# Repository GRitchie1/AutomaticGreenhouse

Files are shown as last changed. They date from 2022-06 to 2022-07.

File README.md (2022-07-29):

# AutomaticGreenhouse

## Introduction
This project is to design and build a solar powered outdoor greenhouse that can monitor and control the temperature & humidity of the air as well as automatically water the plants using collected rainwater.

The design of this project is intended to be highly modular, with the ability to chain multiple target nodes (units) together to allow for data to be combined and analysed by a single controller node.  The power supply from the solar power system will also be chained to allow for a more simple power distribution setup.

## Contents
| Topic | Description |
|---|---|
| [Design](#design) | An overview of the design of the project |
| [Monitoring](#monitoring) | An overview of the design of the project |
| [Parts Lists](#parts-lists) | Up to date parts lists for the project |
| [PCBs](#pcbs) | Information regarding the design and manufacture of the custom printed circuit boards |
| [Networking](#networking) | Information regarding the communication between the target nodes and the controller node. |

## Design
Each target node in the system will be based upon a Raspberry Pi Pico and all hardware interfacing will be done using a custom PCB.  The controller node will be a Raspberry Pi 4 managed using [Balena](https://www.balena.io/).  Communication between the target nodes and the controller node is documented in [networking](#networking).

Each node will feature space for 6 planters, and will have a modular irrigation system to allow for planters to be easily added and removed.

Each node will feature the following sensors:
- Temperature
- Air Humidity
- Soil moisture sensors (1 per planter)
- Light Level (front and back of unit)
- Water level to monitor irrigation system
- Camera (optional: adds ability to implement timelapses and machine learning)

Each node will feature the following control systems:
- Light (LED strips)
- Temperature/Humidity (DC Fan)
- Soil moisture (Water Solenoid/Pump)

An overview of the system layout can be seen below.
System Overview

## Monitoring 

Currently monitoring is done using InfluxDB and Grafana running on a Raspberry Pi 4B.  This is also running an MQTT broker and is using Node-Red to recieve and sanitize the telemetry before inserting it into InfluxDB.

The current Grafana dashboard can be seen below.



## Parts Lists

**Note the following parts lists are not complete and may change.**

The following parts are required to build one node PCB.

| Part | Qty | Description |
|---|-----|---|
| [Pi Pico](https://thepihut.com/products/raspberry-pi-pico) | 1  |The microcontroller used to control the node. |
| [TCA9548A I2C Multiplexer](https://thepihut.com/products/adafruit-tca9548a-i2c-multiplexer)  | 1  | I2C multiplexer to allow connection of up to 8 soil humidity sensors with the same I2C address  |
| N-Channel Mosfet | 5 | Control outputs |

The following sensors are required to build one node.

| Sensor | Qty | Description |
|---|-----|---|
| [Temperature/Humidity](https://thepihut.com/products/adafruit-sensiron-sht31-d-temperature-humidity-sensor-breakout) | 1 | Monitor air temperature and humidity in the greenhouse. |
| [Soil Humidity](https://thepihut.com/products/adafruit-stemma-soil-sensor-i2c-capacitive-moisture-sensor-ada4026) | 6 | Monitor soil humidity of each planter. |
| Light Sensor | 2 | Monitor wavelengths of light to optimise growth. |
| Water Level Switch | 1 | Monitor the stored water level to trigger an alert if it gets too low. |

## PCBs
The PCBs are designed in [EASYEDA](https://easyeda.com/) and can be ordered from [JLC PCB](https://jlcpcb.com/).

The parts for the PCBs can be found in the [Parts Lists](#parts-lists).

## Networking
The communication between the target nodes and the controller node will be handled using MQTT over Ethernet.

The controller node will act as an MQTT broker and also as a client.  Each of the target nodes will be provisioned with unique ID's by the controller node using the following procedure:
1. Target node generates random ID, uses this as Client ID
2. Target node sends "Connection Request" mqtt message to the controller node on topic greenhouse/{Client ID/connection.
3. Target node begins listening on topic greenhouse/{Client ID}/response
4. The Controller node verifies the target node can connect, and returns a new production ID on the topic greenhouse/{Client ID}/response
5. The Target node stores this production ID in the EEPROM and uses this as it's client ID

This procedure ensures that the Controller node can always identify the Target node even after restarts.  It also means that if a Target node PCB is replaced, the new Target node PCB can be programmed with the correct client ID so that the data remains consistent for that unit.

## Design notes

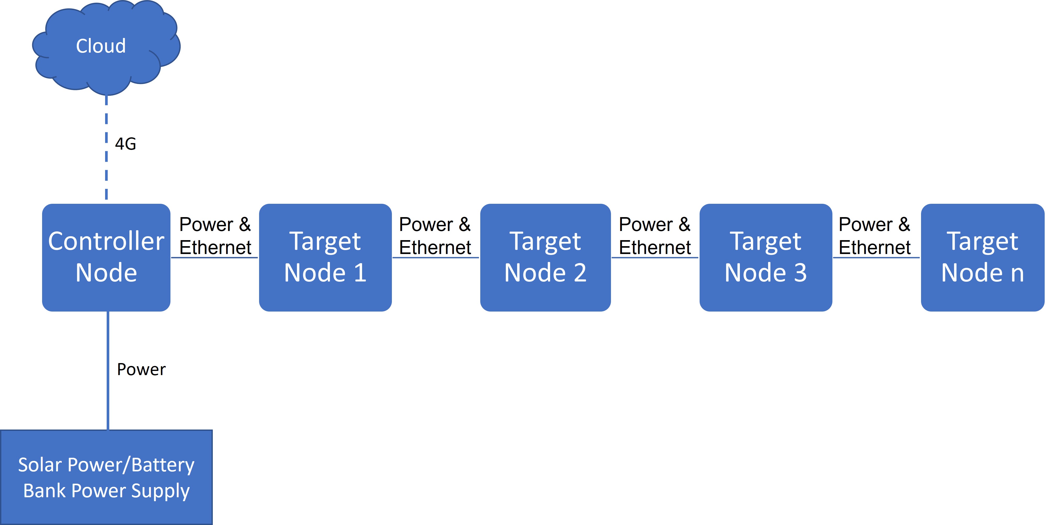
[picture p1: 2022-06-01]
Images/System Overview.jpg

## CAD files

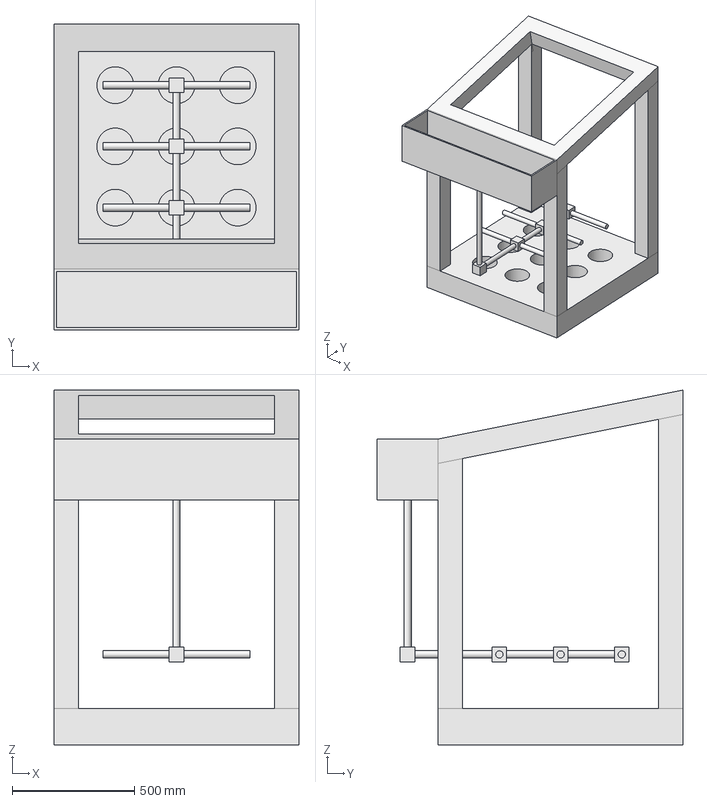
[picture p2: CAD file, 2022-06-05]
3D Model/Frame.FCStd
1000.0 x 1250.0 x 1450.0 mm

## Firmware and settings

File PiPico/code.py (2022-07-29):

import time
import board
import adafruit_sht31d
import busio
import digitalio
import json
import adafruit_veml7700
import adafruit_tca9548a
from adafruit_seesaw.seesaw import Seesaw

#Setup
deviceID = "AutoGH_1"
control = {
            'minSoilHumid':500,
            'maxAirHumid':70
            }


### MQTT ###
from adafruit_wiznet5k.adafruit_wiznet5k import *
import adafruit_wiznet5k.adafruit_wiznet5k_socket as socket
import adafruit_minimqtt.adafruit_minimqtt as MQTT

#Ethernet
##SPI0
SPI0_SCK = board.GP18
SPI0_TX = board.GP19
SPI0_RX = board.GP16
SPI0_CSn = board.GP17


##reset
W5x00_RSTn = board.GP20

pubTopic = 'AutoGH/data'
subTopic = 'AutoGH/control'
mqtt_client = MQTT.MQTT(
    broker="192.168.1.109",  #setup your PC IP address.
    username="iotdash",
    password="iotdash",
    is_ssl=False,
    socket_pool=None,
    ssl_context=None,
    keep_alive=60,
)

def recieveMessage(client, topic, newControl):
    global control
    newControl = json.loads(newControl)
    if newControl != control:
        control = newControl

MY_MAC = (0x00, 0x01, 0x02, 0x03, 0x04, 0x05)
IP_ADDRESS = (192, 168, 1, 100)
SUBNET_MASK = (255, 255, 255, 0)
GATEWAY_ADDRESS = (192, 168, 1, 1)
DNS_SERVER = (8, 8, 8, 8)

ethernetRst = digitalio.DigitalInOut(W5x00_RSTn)
ethernetRst.direction = digitalio.Direction.OUTPUT

cs = digitalio.DigitalInOut(SPI0_CSn)

spi_bus = busio.SPI(SPI0_SCK, MOSI=SPI0_TX, MISO=SPI0_RX)

ethernetRst.value = False
time.sleep(1)
ethernetRst.value = True

eth = WIZNET5K(spi_bus, cs, is_dhcp=True, mac=MY_MAC, debug=False)

print("Chip Version:", eth.chip)
print("MAC Address:", [hex(i) for i in eth.mac_address])
print("My IP address is:", eth.pretty_ip(eth.ip_address))

MQTT.set_socket(socket, eth)

mqtt_client.on_message = recieveMessage

print("Connecting to Broker...")
mqtt_client.connect()

### Sensors ###
i2c = busio.I2C(board.GP5, board.GP4)    #Init I2C

tempHumid = adafruit_sht31d.SHT31D(i2c)
veml7700 = adafruit_veml7700.VEML7700(i2c)

#Soil Sensors
tca = adafruit_tca9548a.TCA9548A(i2c)
numSoilSensors = 3
soilSensors=[Seesaw(tca[i], addr=0x36) for i in range(numSoilSensors)]

### Outputs ###
#Water Pump
pump = digitalio.DigitalInOut(board.GP2)
pump.direction = digitalio.Direction.OUTPUT

#Water Pump
fan = digitalio.DigitalInOut(board.GP3)
fan.direction = digitalio.Direction.OUTPUT

#Vars
loopcount = 0

while True:
    mqtt_client.loop()
    mqtt_client.subscribe(subTopic)
    loopcount += 1

    obj={}
    obj['ID'] = deviceID
    obj['control']=control

    #Env Sensors
    obj['temp'] = tempHumid.temperature
    obj['humid'] = tempHumid.relative_humidity
    obj['light'] = veml7700.light

    #Read Soil Sensors
    soilData = []
    totalSoilHumid = 0
    for sensor in soilSensors:
        soilObj = {}
        soilObj['soilMoisture'] = sensor.moisture_read()
        soilObj['soilTemp'] = sensor.get_temp()
        soilData.append(soilObj)
        totalSoilHumid += soilObj['soilMoisture']
    avgSoilHumid = totalSoilHumid/numSoilSensors
    obj['soil'] = soilData

    #Control outputs
    if avgSoilHumid < control['minSoilHumid']:
        pump.value = True
    else:
        pump.value = False

    if obj['humid'] > control['maxAirHumid']:
        fan.value = True
    else:
        fan.value = False

    #Output States
    obj['pump'] = int(pump.value)
    obj['fan'] = int(fan.value)

    packet = json.dumps(obj)
    mqtt_client.publish(pubTopic, packet)



    time.sleep(1)

    # every 20 passes turn on the heater for 1 second
    if loopcount >= 20 or tempHumid.heater == True:
        if tempHumid.heater == True:
            tempHumid.heater = False
        else:
            loopcount = 0
            tempHumid.heater = True

print("Disconnecting from %s" % mqtt_client.broker)
mqtt_client.disconnect()

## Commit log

2022-06-05 3D model the frame
    [Frame.FCStd]
2022-07-22 Read from sensors
2022-07-22 Change I2C pins to allow use of UART0
2022-07-29 Add output for pump
2022-07-29 Change pin for pump output
2022-07-29 Make soil sensors easier to add/remove
2022-07-29 Change pump state to integer to work better with grafana
2022-07-29 Add control code for pump and fan
2022-07-29 Add node-red flow
2022-08-02 Add target node PCB
